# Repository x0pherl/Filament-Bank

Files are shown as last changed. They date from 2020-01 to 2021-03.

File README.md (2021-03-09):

# Yet Another Filament Bank

## Why another Filament Buffering Solution?

I wanted a solution that met the following requirements:

- Does a decent job of handling retracting filament (duh)
- Fully 3d printable while ideally using a minimal amount of filament
- Retains maximum visibility of filament in the system
- Easy to change filament

## Bill of Materials

While a focus of this design is maximizing 3d printable parts, there are of course, some parts which you will need that cannot be effectively printed.

- 10x PC4-M6 Quick Fitting Push to Connect PTFE fittings
- 5x 604z bearings
- 2x M3 screws/nuts and bolts for affixing assembled bank to your printer stand (I used spare Prusa parts)
- Enough PTFE Teflon tubing (2mm Inner Diameter(ID) X 4mm Outer Diameter (OD)) to connect the bank to your printer and filament stands

## License

This project is licensed under the terms of the  [MIT license](LICENSE.txt).

## Step One: Printing Guide

The first step is to print the pieces required for the buffer chambers. You can start from scratch with the .stl files, or printable files for building this out of PLA exist both in pre-arranged .3mf files for PrusaSlicer or gcode files for direct printing from a Prusa i3 MK3S printer.

### Buffering chambers

#### 1x bottom bracket

This is the bottom part that holds the separator walls and sidewalls in place.

I recommend printing this with transparent filament and minimal infill (downloadable gcodes are 5% hexagonal infill). This model is included as part of `brackets_pegs.3mf` and its associated gcode file.

#### 1x top bracket

This holds the tops of the separator walls and sidewalls in place, holds the wheel assemblies in place, and has tabs for hanging the assembly on your printer stand.

I recommend printing this with transparent filament and minimal infill (downloadable gcodes are 5% hexagonal infill). This model is included as part of `brackets_pegs.3mf` and its associated gcode file.

#### 2x side wall

The sidewalls fit into the top and bottom brackets and hold the separator walls in place.

I recommend printing this with transparent filament to allow more visibility to the filament chambers. Printing these with standard settings will create a sturdier chamber, but I recommend printing them with 10% hex infill with no top/bottom layers. This will allow maximum visibility into the buffer chambers. Both copies of this model are included as part of `sidewalls.3mf` and its associated gcode file.

#### 1x side pegs

This model includes four pegs that secure the separator walls into the top and bottom brackets. The longer pegs go into the top bracket. All pegs include threading at the end to hold them securely in place.

I recommend printing this with either 20% gyroid infill or 100% infill. This model is included as part of `brackets_pegs.3mf` and its associated gcode file.

#### 6x separator wall

The separator walls isolate each color of filament into separate chambers.

I recommend printing these with transparent filament to allow more visibility to the filament chambers. Printing these with standard settings will create a sturdier chamber, but I recommend printing them with 10% hex infill with no top/bottom layers. This will allow maximum visibility into the buffer chambers. Both copies of this model are included as part of `separator_wall.3mf` and its associated gcode file.

### Five wheel assemblies

#### 5x filament wheels

This is the wheel that the filament rotates against when the printer is printing.

The default 20% gyroid infill profile is fine here. I recommend printing each of these five wheels in a different color, it will make it easy to tell at a glance which wheel is turning.

This model is included as part of `wheel_and_peg.3mf` and its associated gcode file.

#### 5x thumb pegs

These pegs lock the brackets into place with the buffering chamber.

The default 20% gyroid infill profile is fine here. I recommend printing each of these in a different color as with the five wheels, it will make it easy to tell at a glance which bracket to pull out when you're changing filament

This model is included as part of `wheel_and_peg.3mf` and its associated gcode file.

#### 5x filament wheel mount bottom

This is the bottom half of the bracket that holds the filament wheel in place and connects to the buffering chambers.

I recommend printing these with transparent filament to allow more visibility to the filament chambers, although it will not matter as much with these parts. I recommend printing them with 10% hex infill with no top/bottom layers. This model is included as part of `wheel_assembly.3mf` and its associated gcode file.

#### 5x filament wheel mount top

This is the top half of the bracket that holds the filament wheel in place and connects to the buffering chambers.

I recommend printing these with transparent filament to allow more visibility to the filament chambers, although it will not matter as much with these parts. I recommend printing them with 10% hex infill with no top/bottom layers. This model is included as part of `wheel_assembly.3mf` and its associated gcode file.

#### 5x filament wheel axle

This is the axle that will screw in place, holding the bearing and brackets in place. These are easy to break while assembling, you may find it useful to print some spares.

The default 20% gyroid infill profile is fine here. This model is included as part of `wheel_assembly.3mf` and its associated gcode file.

#### 10x filament wheel connector

You'll need 10 connectors that hold the filament wheel mount brackets together.

The default 20% gyroid infill profile is fine here. This model is included as part of `wheel_assembly.3mf` and its associated gcode file.

## Modifying

Many changes that you would like to make can be made by modifying `src/filament_bank_values.scad`. For example, increasing the thickness of walls for a more solid assembly. If you make improvements to the design, please submit a pull request on github!

## Assembly

YouTube videos of the assemby process are available:

- [Part One - Filament Buffer Assembly](https://youtu.be/NMZ75zq5oWg)
- [Part Two -- Wheel Bracket Assembly](https://youtu.be/zj1OsbUYNdQ)
- [Part Three -- Final Assembly](https://youtu.be/MDklB2XTeAQ)

### Buffering Chamber Assembly

Start with the bottom bracket. It may be helpful to use a utility knife to clean any printing artifacts out of the 6 slots along the bracket. Note that on the one side, next the round hole for the peg, there is a small notch. That side is the "deeper" section, and your separator walls should be aligned to match.

Slide each of the six separator walls into the slots on the bottom bracket. With the notch on the right of the bottom bracket, slide in the two shorter pegs, then use a pair of pliers to give each peg a twist or two clockwise to lock the pegs in place.

Then carefully align one of the sidewalls with the separator walls, and slide it down into the bottom bracket until it is firmly in place. Repeat with the other side.

Align the top bracket with the sidewall and separator walls and slide into place. With the back bracket facing to the right, slide in the two longer pegs, then use a pair of pliers to give each peg a twist or two clockwise to lock the pegs in place.

Congratulations, you've finished the buffering chambers! Why don't you reward yourself with some gummi bears :)

### Wheel Bracket Assembly

First, fit one of the printed axles through the top filament wheel mount (when inserted properly, it will sit flush on the plate). Place this on a flat surface so that the axle is pointing upwards.

Now, push one of the bearings into a the center of a wheel. Push the combined wheel/bearing onto the axle which is facing upwards.

Carefully align the bottom filament wheel mount so that the socket for the axle aligns with the axle, then carefully pick up the assembled bracket and gently turn the axle a bit by hand or using a coin to turn it. TIGHTEN VERY GENTLY, or the axle may break.

> IF the axle breaks, you will need to get the remaining part out of the bottom bracket. Using a utility knife and stabbing the center of the broken axle and turning it is effective in this case.

Once you have the axle in place, insert the two 3d printed connector bolts to hold the top and bottom brackets in place. When all of the screws are in place, make sure they are all flush with the bottom bracket, or the brackets will not all fit into the buffering chamber.

Finally, make sure the wheel spins freely. You may need to carefully push the wheel towards the top or bottom bracket to eliminate friction and allow it to freely turn.

Screw two of the two PTFE tube quick releases into the top of the bracket, and you'll have assembled a wheel bracket.

Repeat 4 more times and then reward yourself with some gummi bears.

## Installation

The top bracket of the buffering chamber has brackets for hanging. Using M3 screws, secure the buffering chamber to a wall or your print stand. Ideally, there should be a short line of travel from the MMU2s unit downward to the buffering chamber.

Insert each of the wheel assemblies into the top bracket. Note that the back should be angled down as you insert them, so that the guide along the back lines up with the protrusion along the back of the top bracket. Then drop the front of the wheel assembly down and secure it with one of the thumb pegs. If you printed the pegs and wheels in five different colors as suggested in the printing instructions, be sure to match them up.

Finally insert PTFE tubing from the back of the wheel assemblies, and run that to your MMU2s unit; and run PTFE tubing from the front of the wheel assemblies to your filament stands.

Now you're ready to print!

## Credit

This is a filament buffering system designed for use with the Prusa MMU2s, but should be easily adaptable to suit similar requirements or MMU2S modifications adding additional filaments.

The original inspiration for this comes from [David Shealey](https://www.thingiverse.com/TNDave/about)'s brilliant design for his [Prusa MMU2 Filament Retract Bank](https://www.thingiverse.com/thing:3373895). His concept of a simple wheel releasing filament into a channel was the first workable buffering system for the MMU2S, as far as I'm concerned. However, this design suffers from two flaws. First, the walls of the chambers were designed to be acrylic plastic -- which had the advantage of being clear, but required some knowlege of working with acrylic.

This led [Piotr Karkovski](https://www.thingiverse.com/Karkovski/about) to create a modified [Fully printable Prusa MMU2 Filament Retract Bank (Buffer)](https://www.thingiverse.com/thing:3670379). This solved the orignial issue, and Piotr's instructions suggested maintaining visibility by using hex infill with no top or bottom layers. This was a very nice innovation, but it didn't help to solve the other issue with Shealey's original design.

Shealy's design relies on a paddle that slides up and down that, as you feed filament in, is supposed to force the filament to return up the other side. While this occasionally worked for me, I found it to be frustating in practice. [Garth Gangaway](https://www.thingiverse.com/GVader/about) set out to solve this problem with a new design, but this again relied on acrylic panels, and I did not like the clipping solution used on this model.

I am super grateful to all of these designers and their innovation. While I haven't used their original designs in creating this project, it certainly wouldn't exist without their original work, especially David Shealey's original design.

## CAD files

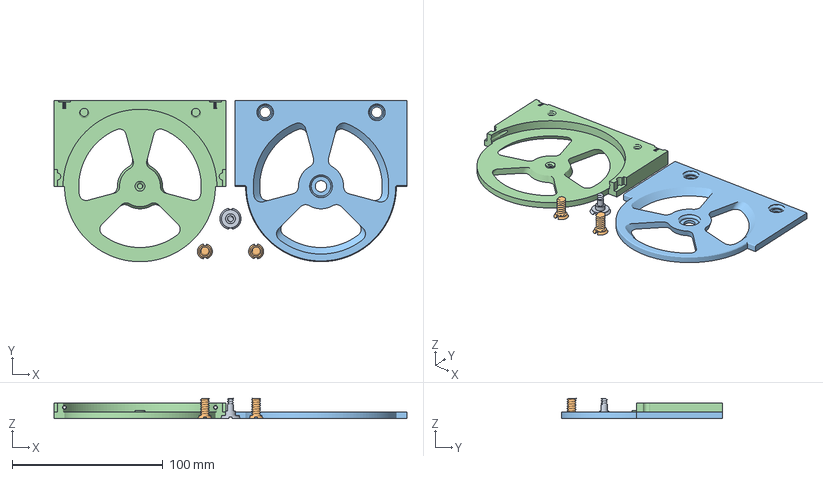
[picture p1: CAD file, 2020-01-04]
printable_3mf/wheel_assembly.3mf
234.0 x 107.0 x 13.5 mm
../stl/axle.stl
../stl/connectors.stl
../stl/filament_wheel_mount_top.stl
../stl/filament_wheel_mount_bottom.stl

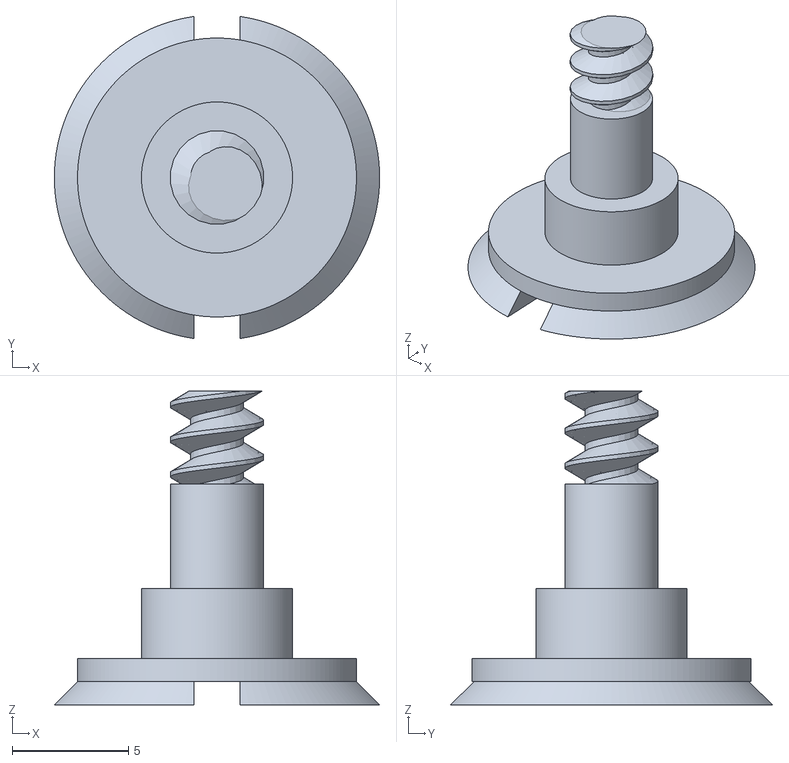
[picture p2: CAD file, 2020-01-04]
stl/axle.stl
14.0 x 13.9 x 13.5

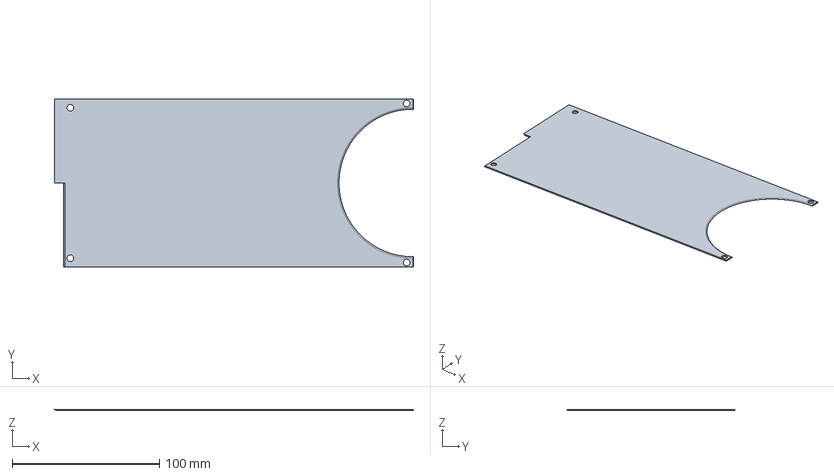
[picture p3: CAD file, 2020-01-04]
printable_3mf/separator_wall.3mf
243.5 x 114.0 x 1.00 mm

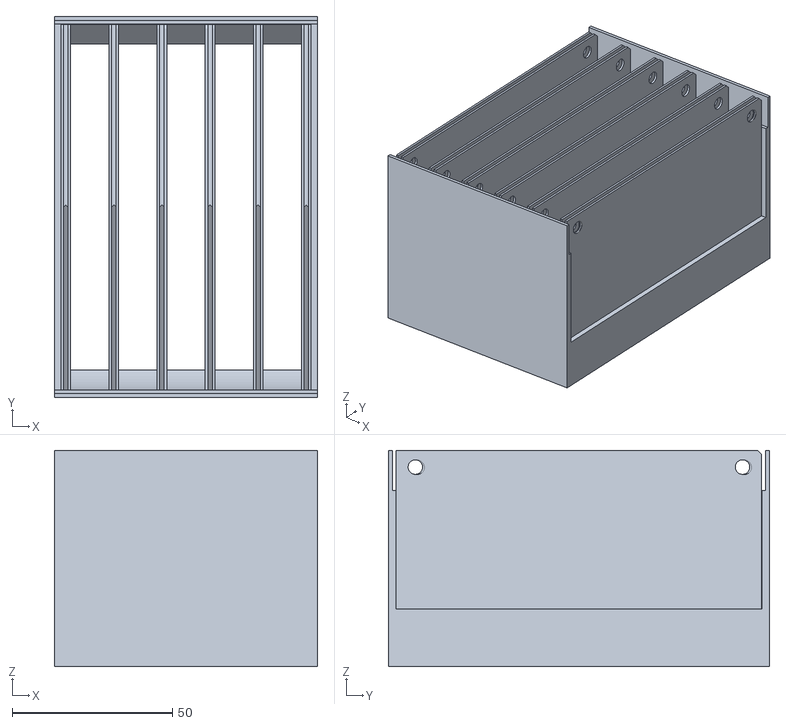
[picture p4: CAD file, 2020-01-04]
stl/bottom_bracket.stl
82.0 x 118.8 x 67.5

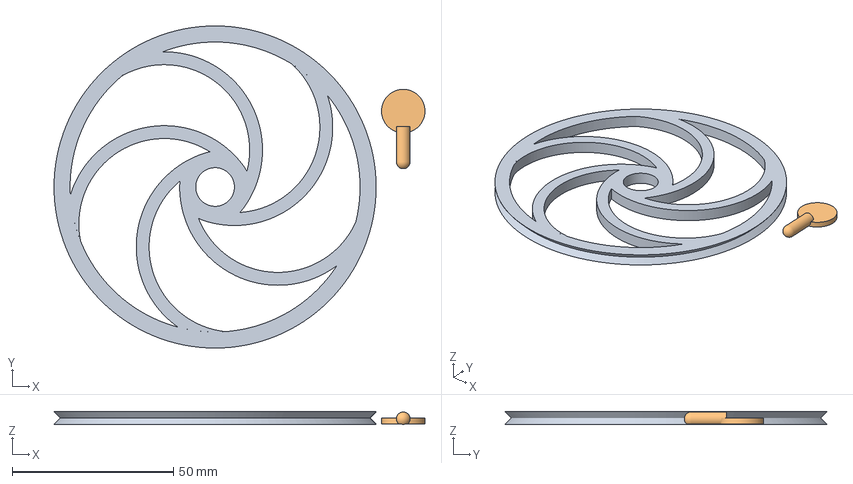
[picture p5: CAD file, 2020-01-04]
printable_3mf/wheel_and_peg.3mf
115.2 x 100.0 x 4.00 mm
../stl/filament_wheel.stl
../stl/thumb_peg.stl

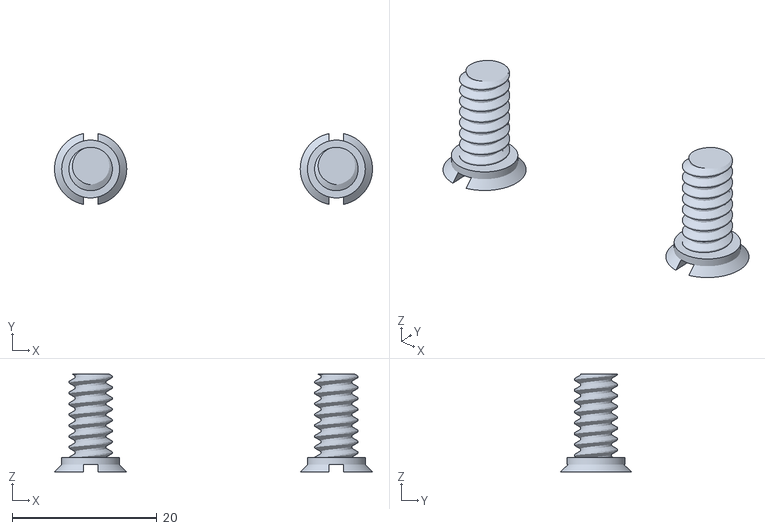
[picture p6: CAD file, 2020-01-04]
stl/connectors.stl
44.0 x 9.80 x 13.5

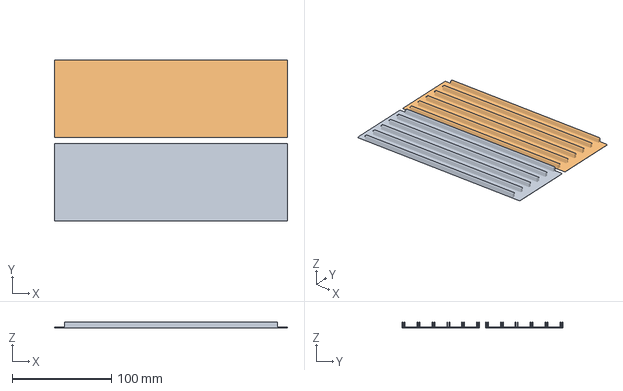
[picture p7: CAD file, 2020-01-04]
printable_3mf/sidewalls.3mf
234.8 x 162.0 x 6.00 mm
../stl/sidewall.stl x 2

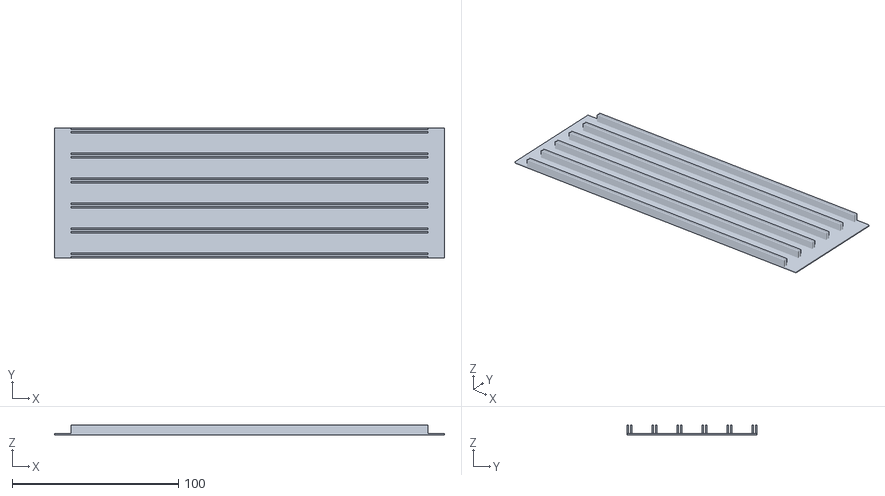
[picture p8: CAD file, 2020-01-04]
stl/sidewall.stl
234.8 x 78.0 x 6.00

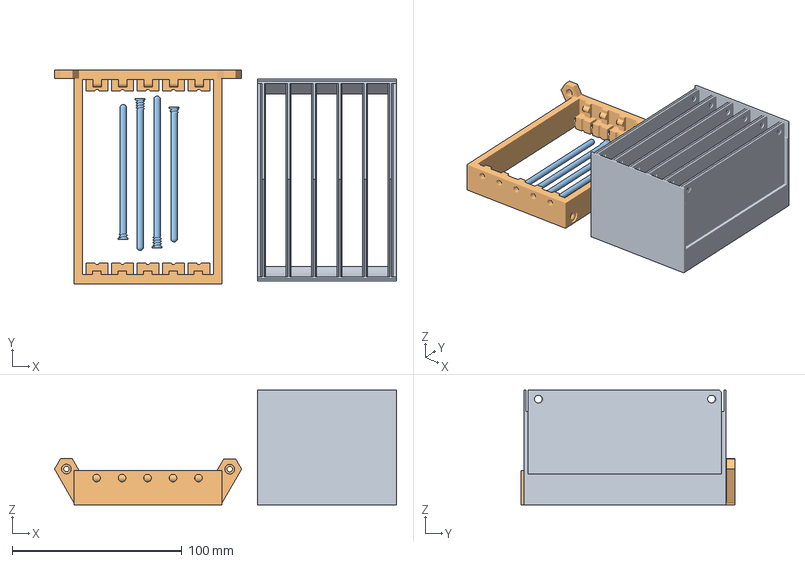
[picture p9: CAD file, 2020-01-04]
printable_3mf/brackets_pegs.3mf
201.4 x 126.0 x 67.5 mm
../stl/bottom_bracket.stl
../stl/top_bracket.stl
../stl/side_pegs.stl

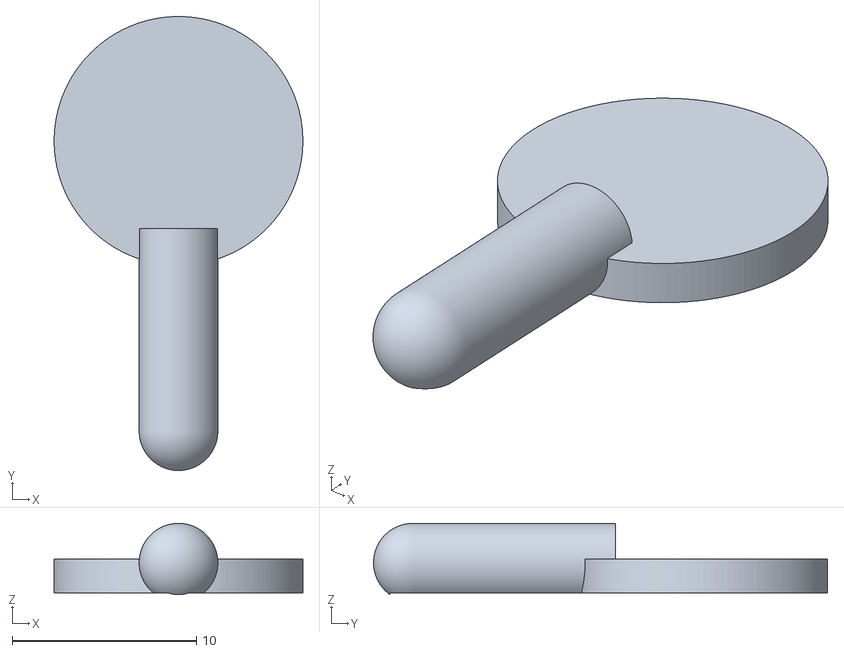
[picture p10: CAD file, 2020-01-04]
stl/thumb_peg.stl
13.5 x 24.6 x 3.87

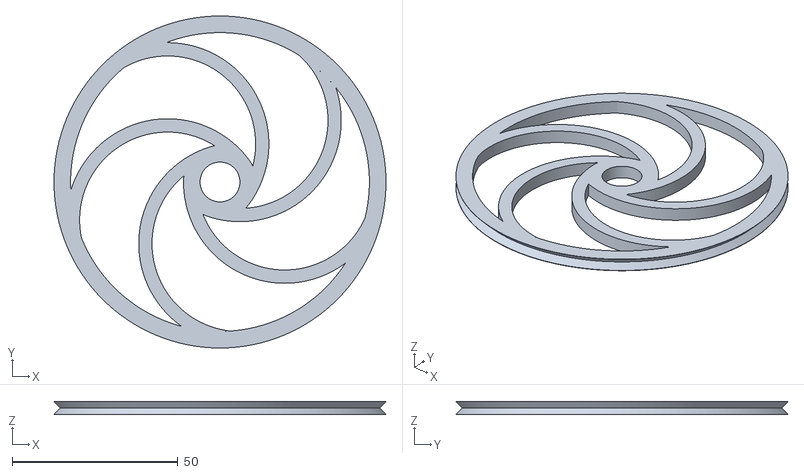
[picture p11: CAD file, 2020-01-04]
stl/filament_wheel.stl
100.0 x 100.0 x 4.00

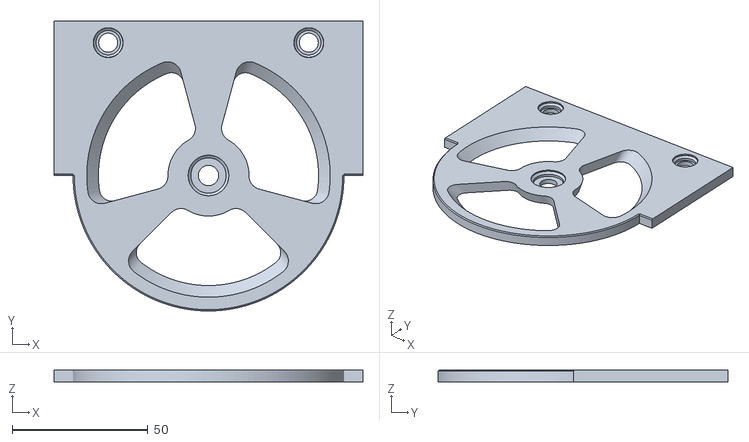
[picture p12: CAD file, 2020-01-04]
stl/filament_wheel_mount_top.stl
114.0 x 107.0 x 4.50

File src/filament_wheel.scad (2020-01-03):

/****************************************************************************
the wheel that the filament bank travels along
*****************************************************************************/
include <filament_bank_values.scad>

wheel(wheel_radius = wheel_radius, axle_radius=bearing_d/2, depth = spoolwheel_thickness, rim_thickness=rim_width, spoke_thickness=spoke_width);


module wheel(wheel_radius=25, axle_radius=10, depth=2, spoke_thickness=2, rim_thickness=2) {
        difference() {
            //rim
            cylinder(r=wheel_radius, h=depth);
            translate([0,0,-1]) 
                cylinder(r=wheel_radius-rim_thickness, h=depth+2);
            //channel for the filament
            translate([0,0, depth/2]) 
                rotate_extrude(convexity = 10)
                    translate([wheel_radius+detail_tolerance/2, 0, 0])
                        circle(r = depth/2, $fn=4);
        }
        
        //axle hub
        difference() {
            cylinder(r=axle_radius+rim_thickness, h=depth);
            translate([0,0,-1]) 
                cylinder(r=axle_radius, h=depth+2);
        }

        //spokes
        for (ii=[0:spoke_count-1]) {
            rotate([0,0,360/spoke_count*ii]) 
                axle(wheel_radius=wheel_radius, axle_radius=axle_radius+rim_width, depth=depth, spoke_thickness=spoke_thickness, rim_thickness=rim_thickness); 
        }
}


module axle(wheel_radius=25, axle_radius=10, depth=2, spoke_thickness=2, rim_thickness=2) {
    axle_length = (wheel_radius+axle_radius)/2;
    difference() {
        translate([axle_length-axle_radius,0,0])
            difference() {
                cylinder(r=axle_length, h=depth);
                translate([0,0,-1]) 
                    cylinder(r=axle_length-spoke_thickness, h=depth+2);
                translate([-wheel_radius,0,-1]) 
                    cube([wheel_radius*2, wheel_radius*2, depth+2]);
            }
        //cut off the part that extends into the rim
        difference() {
            cylinder(r=wheel_radius+2, h=depth);
            translate([0,0,-1]) 
                cylinder(r=wheel_radius-rim_thickness, h=depth+2);
        }
    }            
}

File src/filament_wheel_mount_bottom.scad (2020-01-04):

/****************************************************************************
this is the bottom of the bracket that holds the wheel and
festo mounts
*****************************************************************************/
include <filament_bank_values.scad>
use <../lib/iso-threads.scad>
include <festo.scad>
include <wheelcut.scad>
use <axle.scad>
use <connectors.scad>

//for faster rendering, prevent rendering of threads
//must be set to false for printed part
avoid_threads=false;

module solid() {
    //wheel mount
    cylinder(r=wheel_radius, h=separator_wall_width);

    //bearing mount
    cylinder(r=bearing_shelf_d/2, h=separator_wall_width+gap);

    //top peice
    difference() {
        translate([-top_inner_length/2,0,0]) 
            cube([top_inner_length, top_inner_length/2, section_width-separator_wall_width]);
        translate([0,0,separator_wall_width]) 
            cylinder(r=wheel_radius+gap, h=section_width);
        }   
}

module cut() {
    translate([0,0,separator_thickness]) { 
        if (avoid_threads) {
            cylinder(r=bearing_inner_d/2, h=section_width);
        }
        else {
            metric_thread(diameter=bearing_inner_d+1, pitch=1.5, length=section_width, internal=true);
        }
    }
    translate([-wheel_radius,top_inner_length/2-(festo_length+festo_sink_depth)/2,section_width/2]) 
        festo_opening(simplify=avoid_threads);
    translate([wheel_radius,top_inner_length/2-(festo_length+festo_sink_depth)/2,section_width/2]) 
        festo_opening(simplify=avoid_threads);
    translate([-(wheel_radius-gap-wall_thickness*2),wheel_radius-gap,-(separator_thickness*2-2-section_width/2)]) 
        rotate([180,0,0]) 
            translate([0,0,separator_thickness*2-2-section_width/2])
                //scale([1.1,1.1,1]) 
                connector(simplify=avoid_threads, internal=true);
    translate([wheel_radius-gap-wall_thickness*2,wheel_radius-gap,-(separator_thickness*2-2-section_width/2)]) 
        rotate([180,0,0]) 
            translate([0,0,separator_thickness*2-2-section_width/2])
                //scale([1.1,1.1,1]) 
                connector(simplify=avoid_threads, internal=true);
    translate([0,0,-detail_tolerance/2]) 
        wheelcut(wheel_radius, 5, 5, 10, separator_wall_width+detail_tolerance, 90, 0);
    translate([top_inner_length/2-separator_wall_width/2,-1,separator_wall_width]) {
        cube([separator_wall_width,wall_thickness*2,section_width-separator_wall_width*2+1]);
    translate([0,wall_thickness*2-separator_wall_width,0])
        cylinder(r=separator_wall_width/2, h=section_width-separator_wall_width*2+1);
    }
    translate([-wheel_radius-gap-wall_thickness-separator_wall_width/2,-1,separator_wall_width]) {
        cube([separator_wall_width,wall_thickness*2,section_width-separator_wall_width*2+1]);
    translate([separator_wall_width,wall_thickness*2-separator_wall_width,0])
        cylinder(r=separator_wall_width/2, h=section_width-separator_wall_width*2+1);
    }
    edge_chamfer();
}

difference() {
    solid();
    cut();
}

//preview of the wheel placement
if (avoid_threads) {
    %translate([0,0,section_width/2]) 
        cylinder(r=wheel_radius, h=spoolwheel_thickness, center=true);
}

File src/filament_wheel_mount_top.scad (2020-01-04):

/****************************************************************************
this is the top of the bracket that holds the wheel and
festo mounts
*****************************************************************************/
include <filament_bank_values.scad>
use <connectors.scad>
use <axle.scad>
include <festo.scad>
include <wheelcut.scad>
use <../lib/iso-threads.scad>

translate([0,0,separator_wall_width]) {
    rotate([0,180,0]) 
        filament_wheel_mount_top();
}

module filament_wheel_mount_top() {
    difference() {
        union() {
            translate([-top_inner_length/2,0,0]) 
                cube([top_inner_length, top_inner_length/2, separator_wall_width]);
            cylinder(r=wheel_radius, h=separator_wall_width);
        }
        translate([0,0,-detail_tolerance/2]) 
            wheelcut(wheel_radius, 5, 5, 10, separator_wall_width+detail_tolerance, 90, 0);
        translate([-wheel_radius,top_inner_length/2-(festo_length+festo_sink_depth)/2,section_width/2]) 
            scale(1.2) festo_opening(simplify=true);
        translate([wheel_radius,top_inner_length/2-(festo_length+festo_sink_depth)/2,section_width/2]) 
            scale(1.2) festo_opening(simplify=true);
        //sink the axle down a little to provide some buffer
        cylinder(r=bearing_d/2+gap+.5, h=1.02, center=true);
        translate([0,0,0.5]) 
            axle_solid(simplify=true, internal=true);
        translate([-(wheel_radius-gap-wall_thickness*2),wheel_radius-gap,0]) {
            cylinder(r=bearing_d/4+gap*2+.5, h=1.2, center=true);
            translate([0,0,0.5]) 
                connector(simplify=true, internal=true);
        }
        translate([wheel_radius-gap-wall_thickness*2,wheel_radius-gap,0]) {
            cylinder(r=bearing_d/4+gap*2+.5, h=1.2, center=true);
            translate([0,0,0.5])
                connector(simplify=true, internal=true);
            }
    edge_chamfer();
    }
}

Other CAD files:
src/wheelcut.scad
src/axle.scad
src/bottom_bracket.scad
src/connectors.scad
src/festo.scad
src/filament_bank_values.scad
src/separator_wall.scad
src/side_pegs.scad
src/sidewall.scad
src/thumb_peg.scad
src/top_bracket.scad
stl/separator wall.stl
stl/separator_wall.stl

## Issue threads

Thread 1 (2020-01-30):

Build script 3mf generation is not arranging parts properly on plate

x0pherl, 2020-01-30:
Need to identify proper prusa-slicer-console parameters for arranging sheets without manual correction. The prusaslicer documentation doesn't cover console usage well, but https://manual.slic3r.org/advanced/command-line is probably relevant

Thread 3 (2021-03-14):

separator_wall into bottom_bracket clearance

zxcv-org, 2021-03-14:
It might be worth leaving a little more space in the bottom_bracket for the separator_wall to plug in.

1. The separator_wall bottom seems to bump down for 50% of the bottom distance, while the bottom_bracket seems to have space for the separator_wall that's 50% of the same bottom distance.  I experienced (on a reasonably-well-tuned MK3S+) a clearance problem between the separator_wall and bottom_bracket, where the lower portion wouldn't quite plug in without some delicate trimming.
2. The upper portion of the trough in the bottom_bracket seems to allow the separator_wall to float out slightly beyond the end of the overall separator_wall slot, which is helpful for clearance purposes, while the lower portion of the trough in the bottom_bracket ends "early" due to some material that I guess is the lower portion of the support for the sidewall.  It might make sense to allow the separator_wall to poke out a little more by notching a little more room there for each separator_wall (or whatever works to give a tad more room).  I think a fix for 1 above would still be needed to get the separator_wall bottom holes to line up with corresponding bottom_bracket holes though.

Both 1 and 2 are fairly easy to work around using some small wire snips, but the snipping tends to crack the side wall perimeter (which doesn't immediately seem to cause any functional problem).  Carefully snipping 5 separator_wall(s) is a little tedious, but it works.

Thanks for designing this and making it open.  It's been pretty interesting looking through the scad files, but I'm still super new to scad; I didn't immediately see an easy way to achieve the clearance.  I might try again later and maybe send a pull request if I'm sure I found a way, if you haven't already tweaked the clearance by then.  I'm looking forward to trying it out with the MMU2S.

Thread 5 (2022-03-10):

thank you for sharing this

gplv2, 2022-03-10:
Not an issue but a thank you.  This is really awesome stuff.  Thanks for sharing this completely, it's more than just a filament bank, it's a lesson on how to use openSCAD as well.

I'm printing parts now, looks really good.   Perhaps the only thing I was looking for but not found immediately is the layer height for each part.   (assuming the wall can be higher and as such print faster).

The wheels are now printed on 0.2mm and they look really good.  getting the bearings here seems a bit problematic if you want to avoid ordering from china.

So again, really really appreciate this.

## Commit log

2020-01-04 added license and completed README. broke apart connector and axle parts
    [axle.scad, axle.stl, axle_connectors.scad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]
2020-01-14 renamed assembly videos folder
2020-01-15 remove duplicate axle stl file
    [spare_axle.stl]
2021-03-05 Fix axle -> connector typo.
